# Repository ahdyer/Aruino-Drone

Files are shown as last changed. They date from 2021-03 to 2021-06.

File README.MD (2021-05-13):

## Arduino-Drone

### Description
STM32 based flight controller, developed as a final year project for the university of bath<br />

### Starting
To download this project to your computer:
1. Install GIT: https://git-scm.com/downloads
1. Go into your main project directory, open commad line and run:<br />
`git clone https://github.com/your_username/TBRe21-TSAL.git` <br />
Alternativley Install https://desktop.github.com/ and setup a local repoistory

### Using Git in Altium
1. **Save:** Once you make any changes, save the file or project
1. **Commit:** Right click on the file or project, then Version Control -> Commit. Add a note what changes you have done. This will be still local until you push the changes. See the next step.
1. **Push:** When you would like to upload all the changes to github, right click on the file / project -> Version Control -> Push
1. **Check:** Go to your github to see if everything was uploaded correctly

### Download the latest changes
If you would like to download the latest files from Github, then:<br />
1. `git fetch` # this will download the latest files from Github to your local computer<br />
2. Alternativley Install https://desktop.github.com/ and press the fetch button

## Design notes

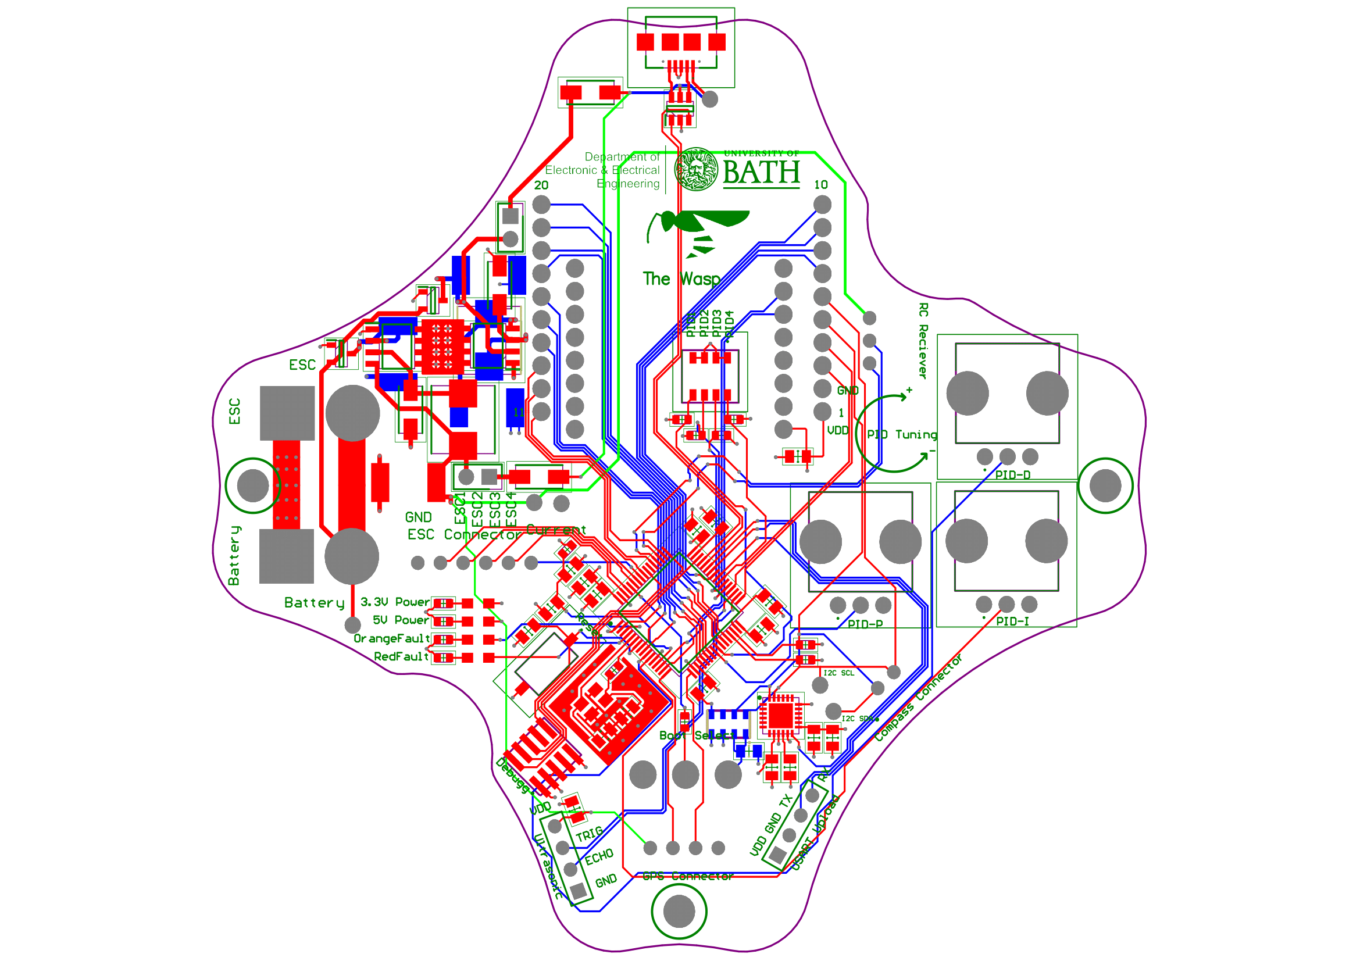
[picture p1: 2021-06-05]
STM32 Flight Controller/Schematic PNGs/STM32 Flight Controller-6.png

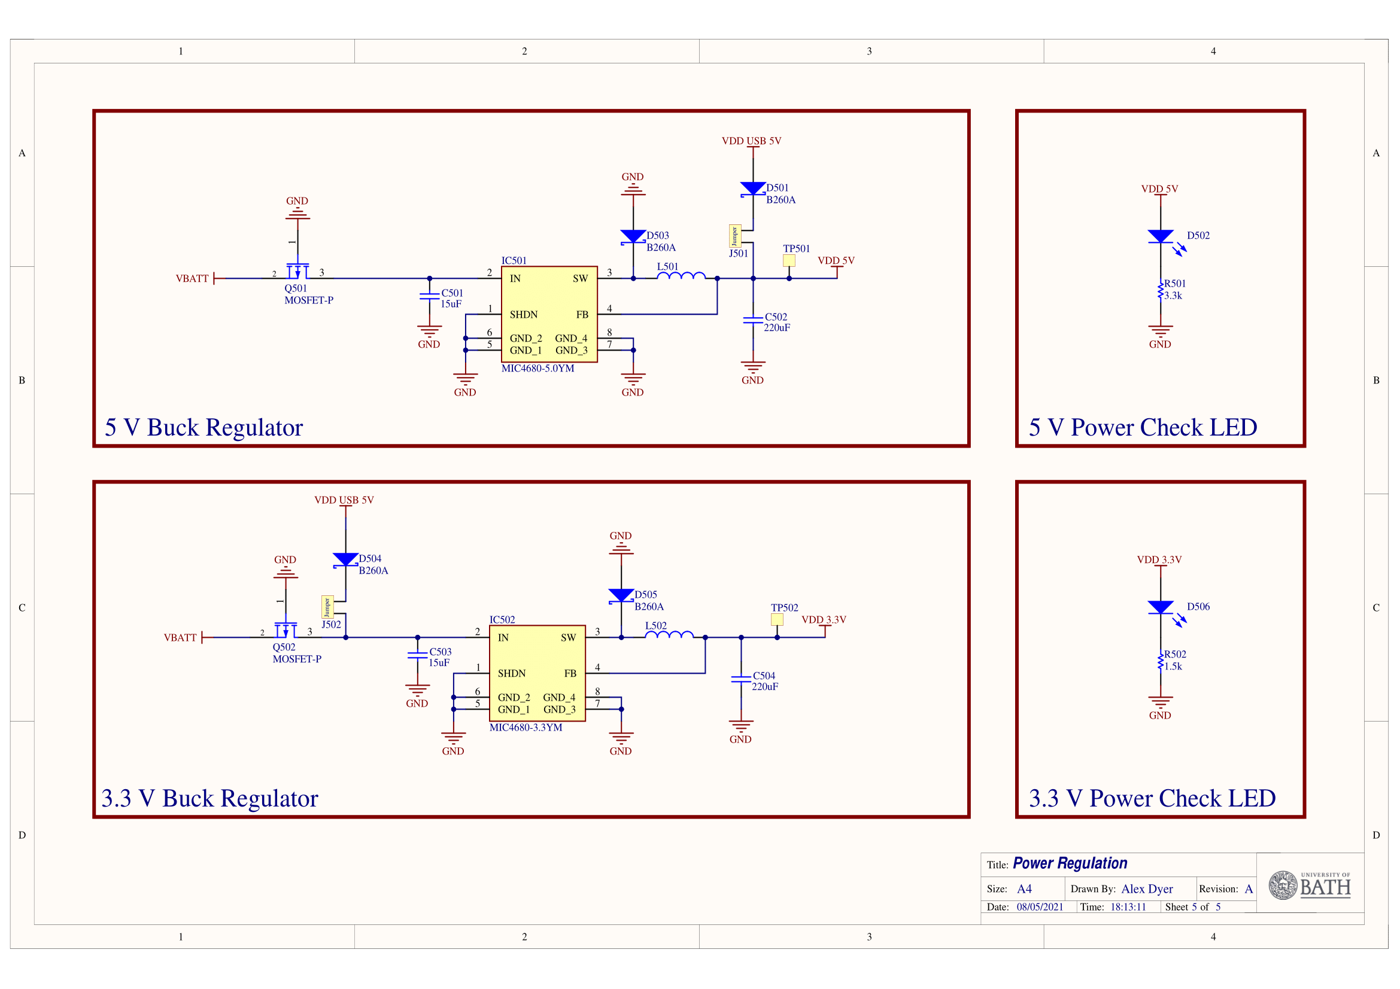
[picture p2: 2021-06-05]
STM32 Flight Controller/Schematic PNGs/STM32 Flight Controller-5.png

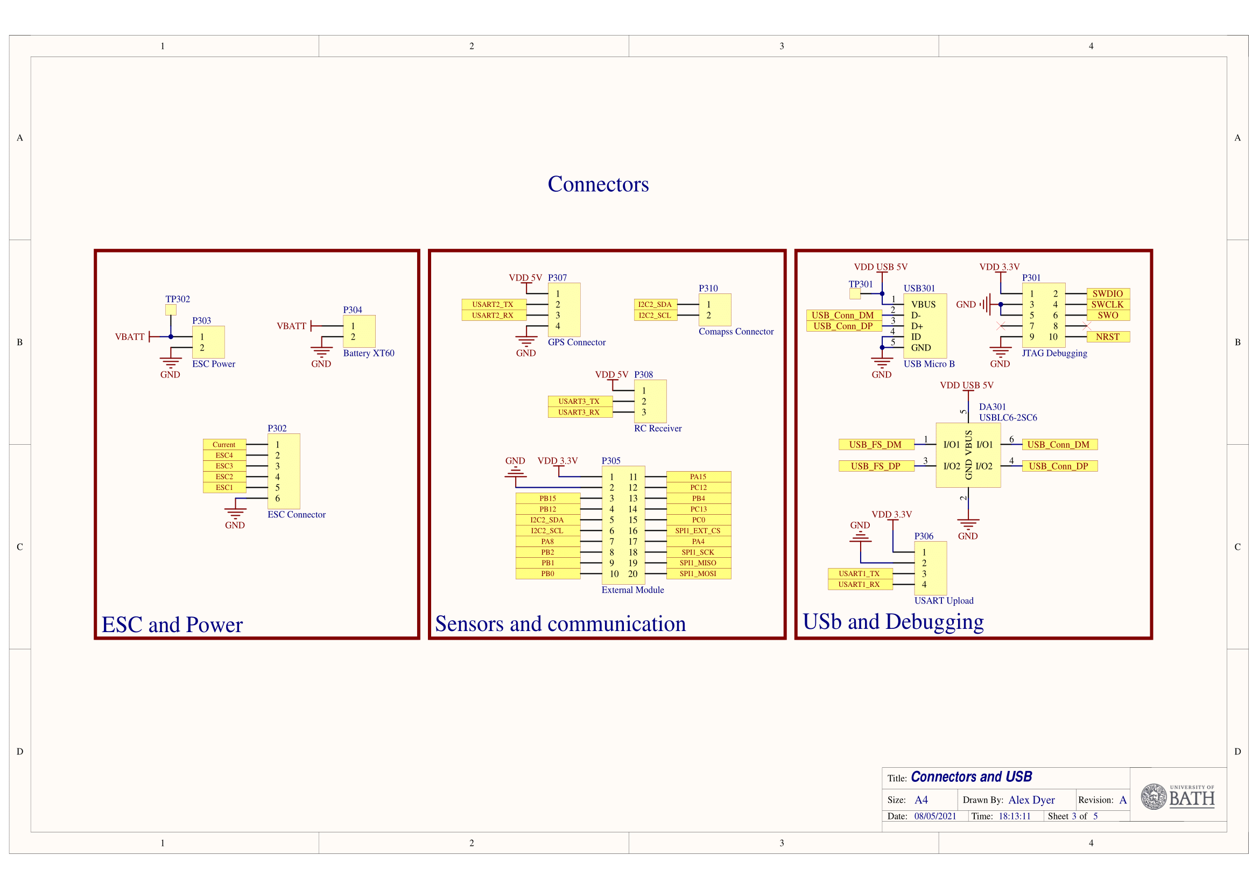
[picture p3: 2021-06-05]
STM32 Flight Controller/Schematic PNGs/STM32 Flight Controller-3.png

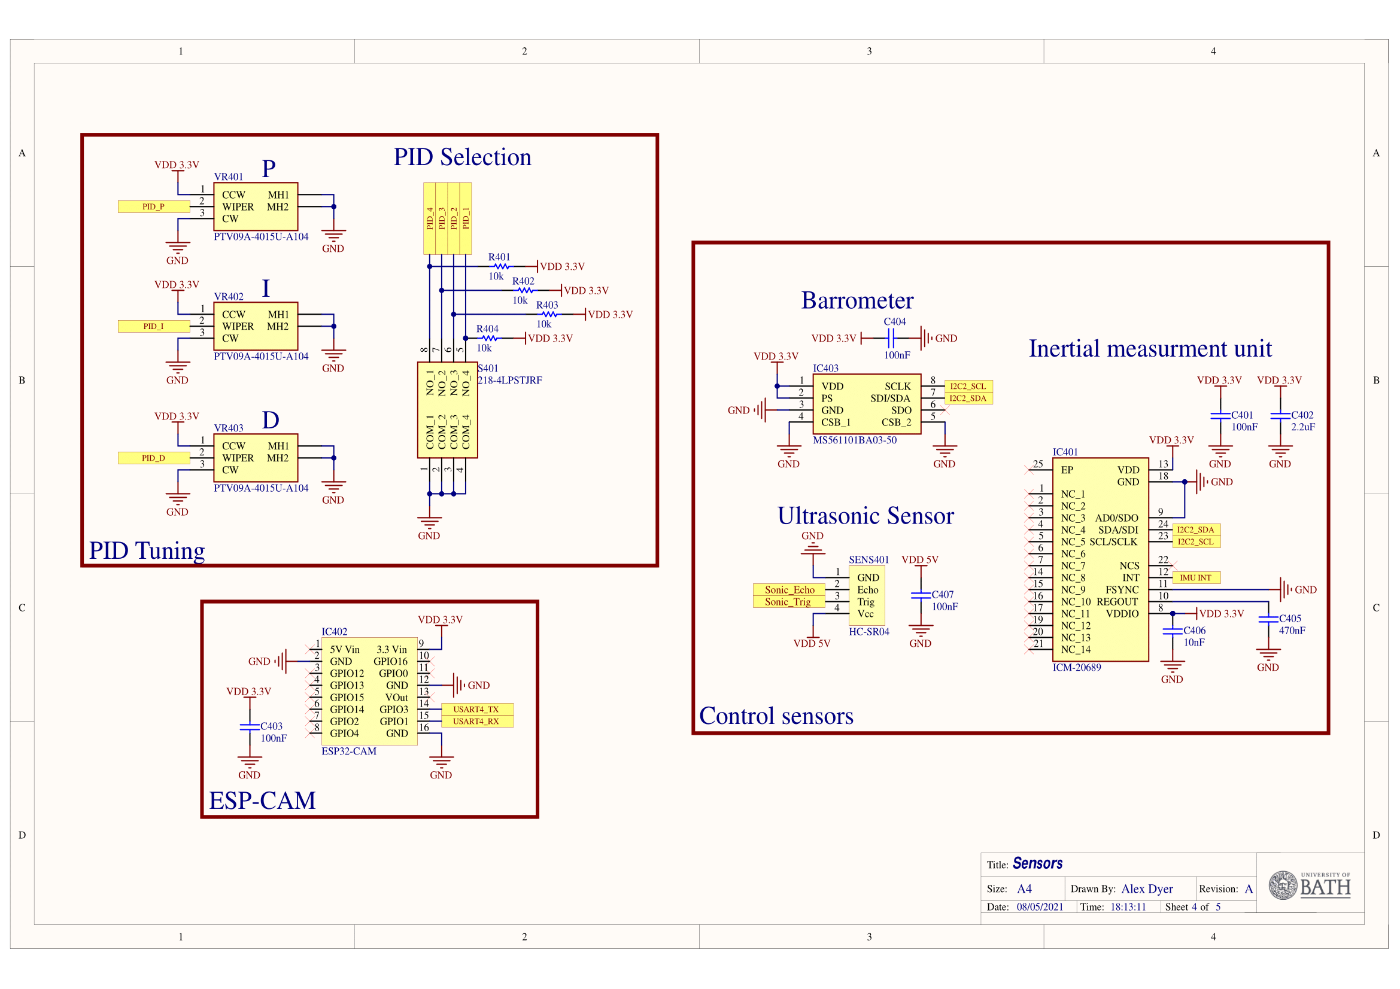
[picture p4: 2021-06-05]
STM32 Flight Controller/Schematic PNGs/STM32 Flight Controller-4.png

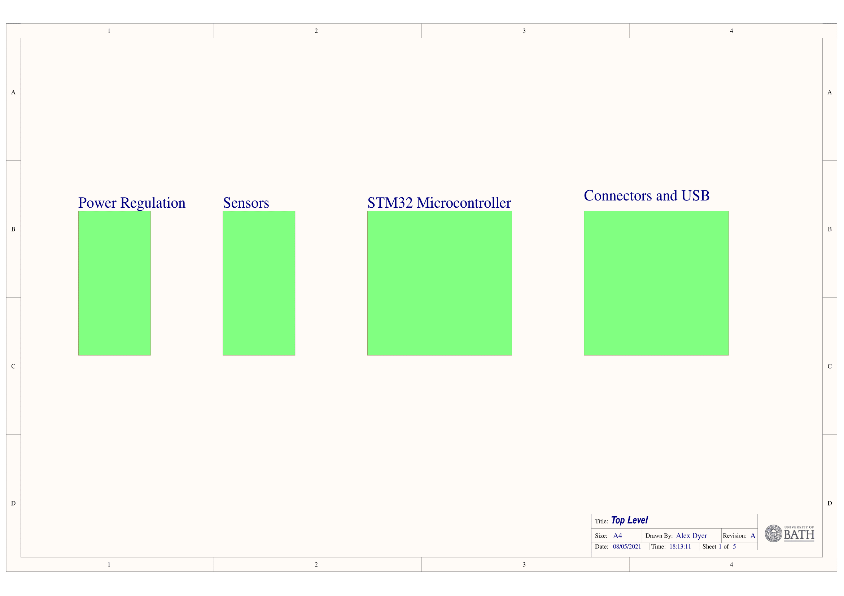
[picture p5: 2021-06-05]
STM32 Flight Controller/Schematic PNGs/STM32 Flight Controller-1.png

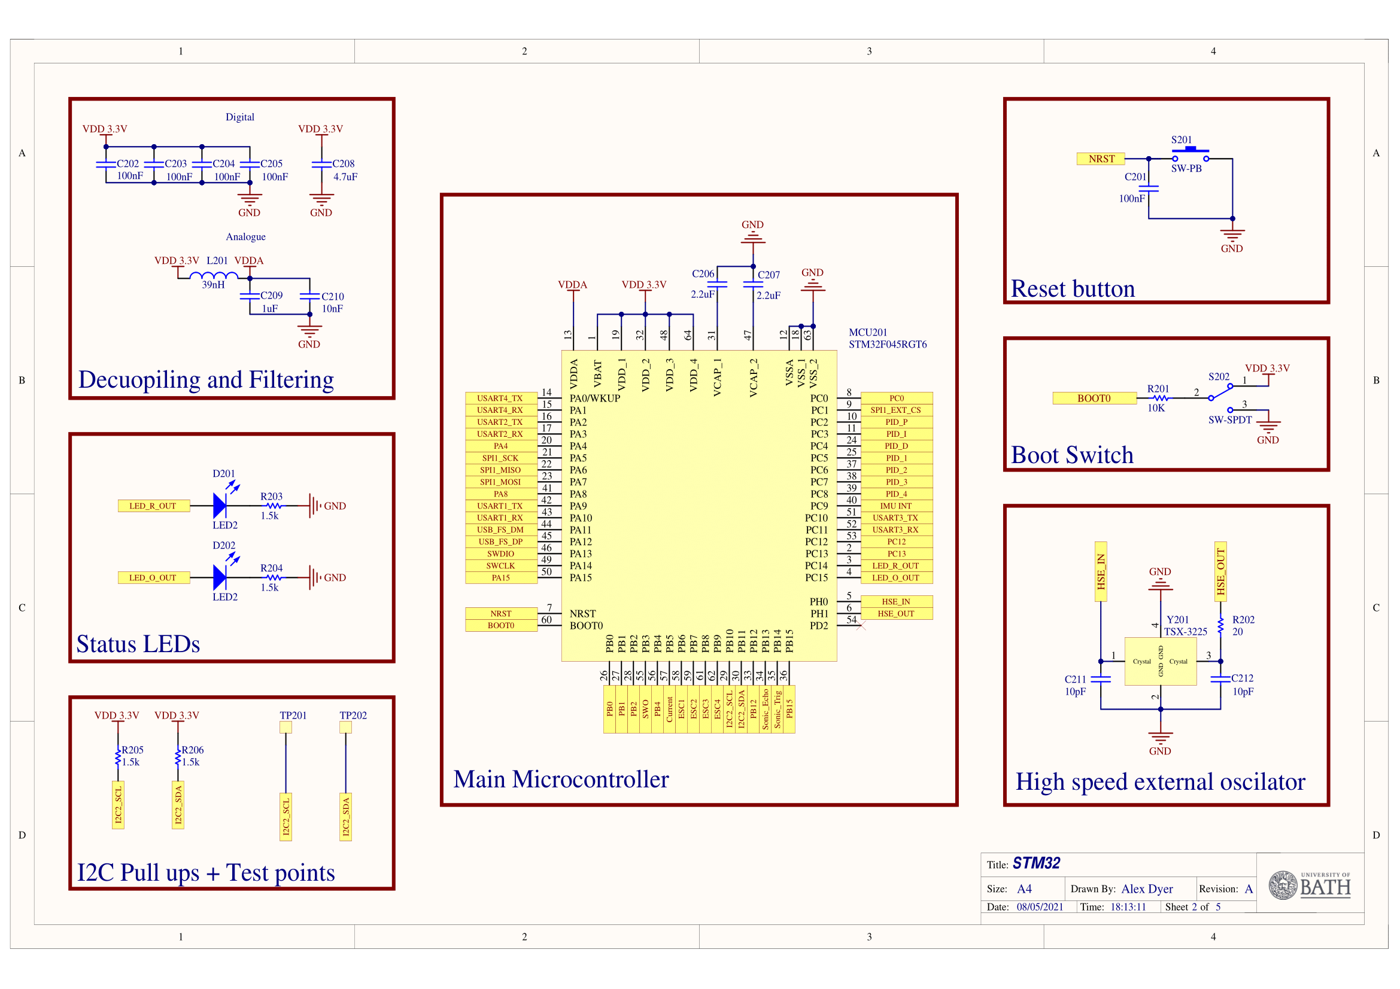
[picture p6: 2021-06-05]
STM32 Flight Controller/Schematic PNGs/STM32 Flight Controller-2.png

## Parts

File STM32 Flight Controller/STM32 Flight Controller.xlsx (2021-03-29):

Comment | Description | Designator | Footprint | LibRef | Quantity | Value | Purchase | TBRe Resistors
Cap | Capacitor | C201, C202, C203, C204, C205, C401, C403, C404, C407 | 0805 Cap | Cap | 9 | 100nF | https://uk.rs-online.com/web/p/mlccs-multilayer-ceramic-capacitors/6480957/
Cap | Low ESR Capacitor | C206, C207, C402 | 0805 Cap | Cap | 3 | 2.2uF | https://uk.rs-online.com/web/p/mlccs-multilayer-ceramic-capacitors/7883048/
Cap | Capacitor | C208 | 0805 Cap | Cap | 1 | 4.7uF | https://uk.rs-online.com/web/p/mlccs-multilayer-ceramic-capacitors/7883041/
Cap | Capacitor | C209 | 0805 Cap | Cap | 1 | 1uF | https://uk.rs-online.com/web/p/mlccs-multilayer-ceramic-capacitors/7883054/
Cap | Capacitor | C210 | 0805 Cap | Cap | 1 | 10nF | https://uk.rs-online.com/web/p/mlccs-multilayer-ceramic-capacitors/6983462/
Cap | Capacitor | C211, C212 | 0805 Cap | Cap | 2 | 10pF | https://uk.rs-online.com/web/p/mlccs-multilayer-ceramic-capacitors/6984033/
Cap | Capacitor | C405 | 0805 Cap | Cap | 1 | 470nF | https://uk.rs-online.com/web/p/mlccs-multilayer-ceramic-capacitors/6480806/
Cap | Capacitor | C406 | 0805 Cap | Cap | 1 | 10nF | https://uk.rs-online.com/web/p/mlccs-multilayer-ceramic-capacitors/6480957/
Cap | Capacitor | C501, C503 | 2917 Cap (TPSE) - duplicate | Cap | 2 | 15uF | https://www.mouser.co.uk/ProductDetail/AVX/TCJD156M050R0150E
Cap | Capacitor | C502, C504 | 2917 Cap (TJSD) | Cap | 2 | 220uF | https://www.mouser.co.uk/ProductDetail/AVX/TPSE227M016R0100V
LED2 | Typical RED, GREEN, YELLOW, AMBER GaAs LED | D201 | SML-211 Series | LED2 | 1 |  | https://uk.rs-online.com/web/p/leds/7007907/
LED2 | Typical RED, GREEN, YELLOW, AMBER GaAs LED | D202, D502, D506 | SML-211 Series | LED2 | 3 |  | https://uk.rs-online.com/web/p/leds/7007897/
B260A | Schottky Diode | D501, D503, D504, D505 | SMA (DO-214AC) | D Schottky | 4 |  | https://www.mouser.co.uk/ProductDetail/Diodes-Incorporated/B260A-13-F?qs=9XwZYT68TnR%252B3fnyovGFLA%3D%3D
USBLC6-2SC6 | TMicroelectronics USBLC6-2SC6, Dual-Element Uni-Directional TVS Diode Array, 6-Pin SOT-23 | DA301 | SOT95P280X145-6N | USBLC6-2SC6 | 1 |  | https://uk.rs-online.com/web/p/tvs-diodes/6247693/
ICM-20689 | Integrated Circuit | IC401 | QFN50P400X400X95-25N-D | ICM-20689 | 1 |  | https://www.mouser.co.uk/ProductDetail/TDK-InvenSense/ICM-20689?qs=u4fy%2FsgLU9NcfLrncAE%252BeQ%3D%3D
ESP32-CAM |  | IC402 | ESP-CAM | ESP-CAM | 1
MS561101BA03-50 | Integrated Circuit Note, Mouser Chepaer | IC403 | MS561101BA03-50 | MS561101BA03-50 | 1 |  | https://uk.rs-online.com/web/p/pressure-sensor-ics/8937130/
MIC4680-5.0YM | Switching Voltage Regulators 1.3A SuperSwitcher (5v) | IC501 | SOIC127P599X173-8N | MIC4680-5.0YM | 1 |  | https://www.mouser.co.uk/ProductDetail/Microchip-Technology-Micrel/MIC4680-50YM-TR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
MIC4680-3.3YM | Integrated Circuit | IC502 | SOIC127P599X173-8N | MIC4680-3.3YM | 1 |  | https://www.mouser.co.uk/ProductDetail/Microchip-Technology-Micrel/MIC4680-33YM?qs=kh6iOki%2FeLEl7qvTxSy9RA==
Jumper |  | J501, J502 | 2.54mm 2 pin Jumper | Jumper | 2 |  | https://www.mouser.co.uk/ProductDetail/Molex/22-28-5027?qs=l%252BWx29wYPrz7EnZr1XjkzQ%3D%3D
Inductor | Inductor | L201 | 0603 | Inductor | 1 | 39nH | https://uk.rs-online.com/web/p/multilayer-surface-mount-inductors/7859212/
Inductor | Inductor | L501, L502 | INDPM7570X540N | Inductor | 2 |  | https://www.mouser.co.uk/ProductDetail/TDK/SPM7054VT-680M-D?qs=BJlw7L4Cy7%2F5GJUhXb8MnA%3D%3D
STM32F045RGT6 |  | MCU201 | QFP50P1200X1200X160-64N | STM32F045RGT6 | 1 |  | https://uk.rs-online.com/web/p/microcontrollers/7926013/
JTAG Debugging | Samtec, FTSH, 10 Way, 2 Row, Straight Pin Header | P301 | TFTSH 1.27mm 10 way | Header 5X2 | 1 |  | https://uk.rs-online.com/web/p/pcb-headers/0451736/
ESC Connector | Header, 6-Pin | P302 | B6B-XH-A | Header 6 | 1 |  | https://uk.farnell.com/jst-japan-solderless-terminals/b6b-xh-a-lf-sn/connector-header-tht-2-5mm-6way/dp/1516282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
ESC Power | Header, 2-Pin | P303 | Female XT60 | Header 2 | 1 |  | https://hobbyking.com/en_us/nylon-xt60-connectors-male-female-5-pairs-genuine.html?___store=en_us
Battery XT60 | Header, 2-Pin | P304 | Female XT60 | Header 2 | 1 |  | https://hobbyking.com/en_us/nylon-xt60-connectors-male-female-5-pairs-genuine.html?___store=en_us
External Module | External Module | P305 | External Module | Header 10X2A | 1 |  | https://www.mouser.co.uk/ProductDetail/Samtec/CES-110-02-G-S?qs=0lQeLiL1qyZeC2zaPJHALg%3D%3D
USART Upload | Header, 4-Pin | P306 | HDR1X4 | Header 4 | 1 |  | https://www.mouser.co.uk/ProductDetail/Amphenol-Commercial-Products/G800W304018EU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
GPS Connector | Header, 4-Pin | P307 | B4B-XH-A | Header 4 | 1 |  | https://uk.farnell.com/jst-japan-solderless-terminals/b4b-xh-a-lf-sn/header-vertical-4way/dp/1516278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
RC Receiver | Header, 3-Pin | P308 | B3B-XH-A | Header 3 | 1 |  | https://uk.farnell.com/jst-japan-solderless-terminals/b3b-xh-a-lf-sn/header-vertical-3way/dp/1516277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
Comapss Connector | Compass Connector | P310 | B2B-XH-A | Header 2 | 1 |  | https://uk.farnell.com/jst-japan-solderless-terminals/b2b-xh-a-lf-sn/header-vertical-2way/dp/1516276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
MOSFET-P | P-Channel MOSFET | Q501, Q502 | SOT95P230X110-3N | MOSFET-P | 2 |  | https://www.mouser.co.uk/ProductDetail/Nexperia/PMV250EPEAR?qs=Yna0arPQ0CTtAa8k6X9CyQ%3D%3D
0603 | Resistor | R201 | 0603 | Res1 | 1 | 10K | https://uk.rs-online.com/web/p/mlccs-multilayer-ceramic-capacitors/2644236/
0603 | Resistor | R202 | 0603 | Res1 | 1 | 20 | https://uk.rs-online.com/web/p/surface-mount-fixed-resistors/6661904/
0603 | Resistor | R203, R204, R205, R206, R502 | 0603 | Res1 | 5 | 1.5k | https://uk.rs-online.com/web/p/mlccs-multilayer-ceramic-capacitors/2644236/
0603 | Resistor | R401, R402, R403, R404 | 0603 | Res1 | 4 | 10k | https://uk.rs-online.com/web/p/surface-mount-fixed-resistors/9013601/
0603 | Resistor | R501 | 0603 | Res1 | 1 | 3.3k | https://uk.rs-online.com/web/p/mlccs-multilayer-ceramic-capacitors/2644236/
SW-PB | Switch | S201 | PTS636SM25JSMTRLFS | SW-PB | 1 |  | https://www.mouser.co.uk/ProductDetail/CK/PTS636-SM25J-SMTR-LFS?qs=vLWxofP3U2zGz0hgscFyyw%3D%3D
SW-SPDT | SPDT Subminiature Toggle Switch, Right Angle Mounting, Vertical Actuation | S202 | Slide Switch | SW-SPDT | 1 |  | https://uk.rs-online.com/web/p/slide-switches/7347334/
218-4LPSTJRF | DIP Switches/SIP Switches SURFACE MOUNT, GOLD, HALF-PITCH DIP SWITCH, 4-POLE, LOW PROFILE ACTUATOR, BOTTOM SEAL, TAPE SEAL, J-BEND, REEL, OFF | S401 | 2184LPSTJRF | 218-4LPSTJRF | 1 |  | https://www.mouser.co.uk/ProductDetail/CTS-Electronic-Components/218-4LPSTJRF
HC-SR04 | Ultrasonic Distance Sensor | SENS401 | HDR1X4 | Header 4 | 1 |  | https://www.sparkfun.com/products/15569
Test Point |  | TP201, TP202, TP301, TP302, TP501, TP502 | Test Point THT 1mm | Test Point | 6 |  | https://uk.rs-online.com/web/p/terminal-posts/2622179/?searchHistory=%7B%22enabled%22%3Atrue%7D\
USB Micro B | Molex USB Connector, SMT, Socket 2.0 B, Solder, Right Angle | USB301 | UJ2MIBHGSMTTR | USB Micro B | 1 |  | https://www.mouser.co.uk/ProductDetail/CUI-Devices/UJ2-MIBH-G-SMT-TR
PTV09A-4015U-A104 | Variable Resistor | VR401, VR402, VR403 | PTV09A4015UA104 | PTV09A-4015U-A104 | 3 |  | https://www.mouser.co.uk/ProductDetail/Bourns/PTV09A-4015U-A104
TSX-3225 | EPSON 16MHz Crystal Unit ±10ppm TSX-3225 4-Pin | Y201 | TSX-3225 | TSX-3225 | 1 |  | https://uk.rs-online.com/web/p/crystal-units/9047516/

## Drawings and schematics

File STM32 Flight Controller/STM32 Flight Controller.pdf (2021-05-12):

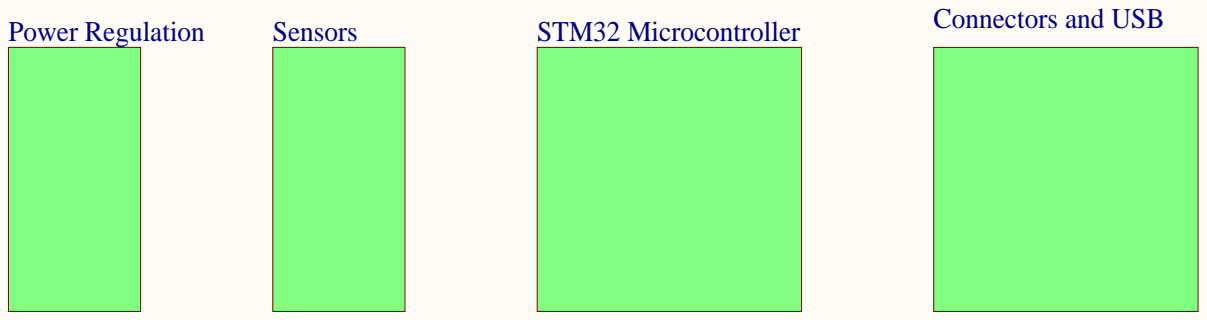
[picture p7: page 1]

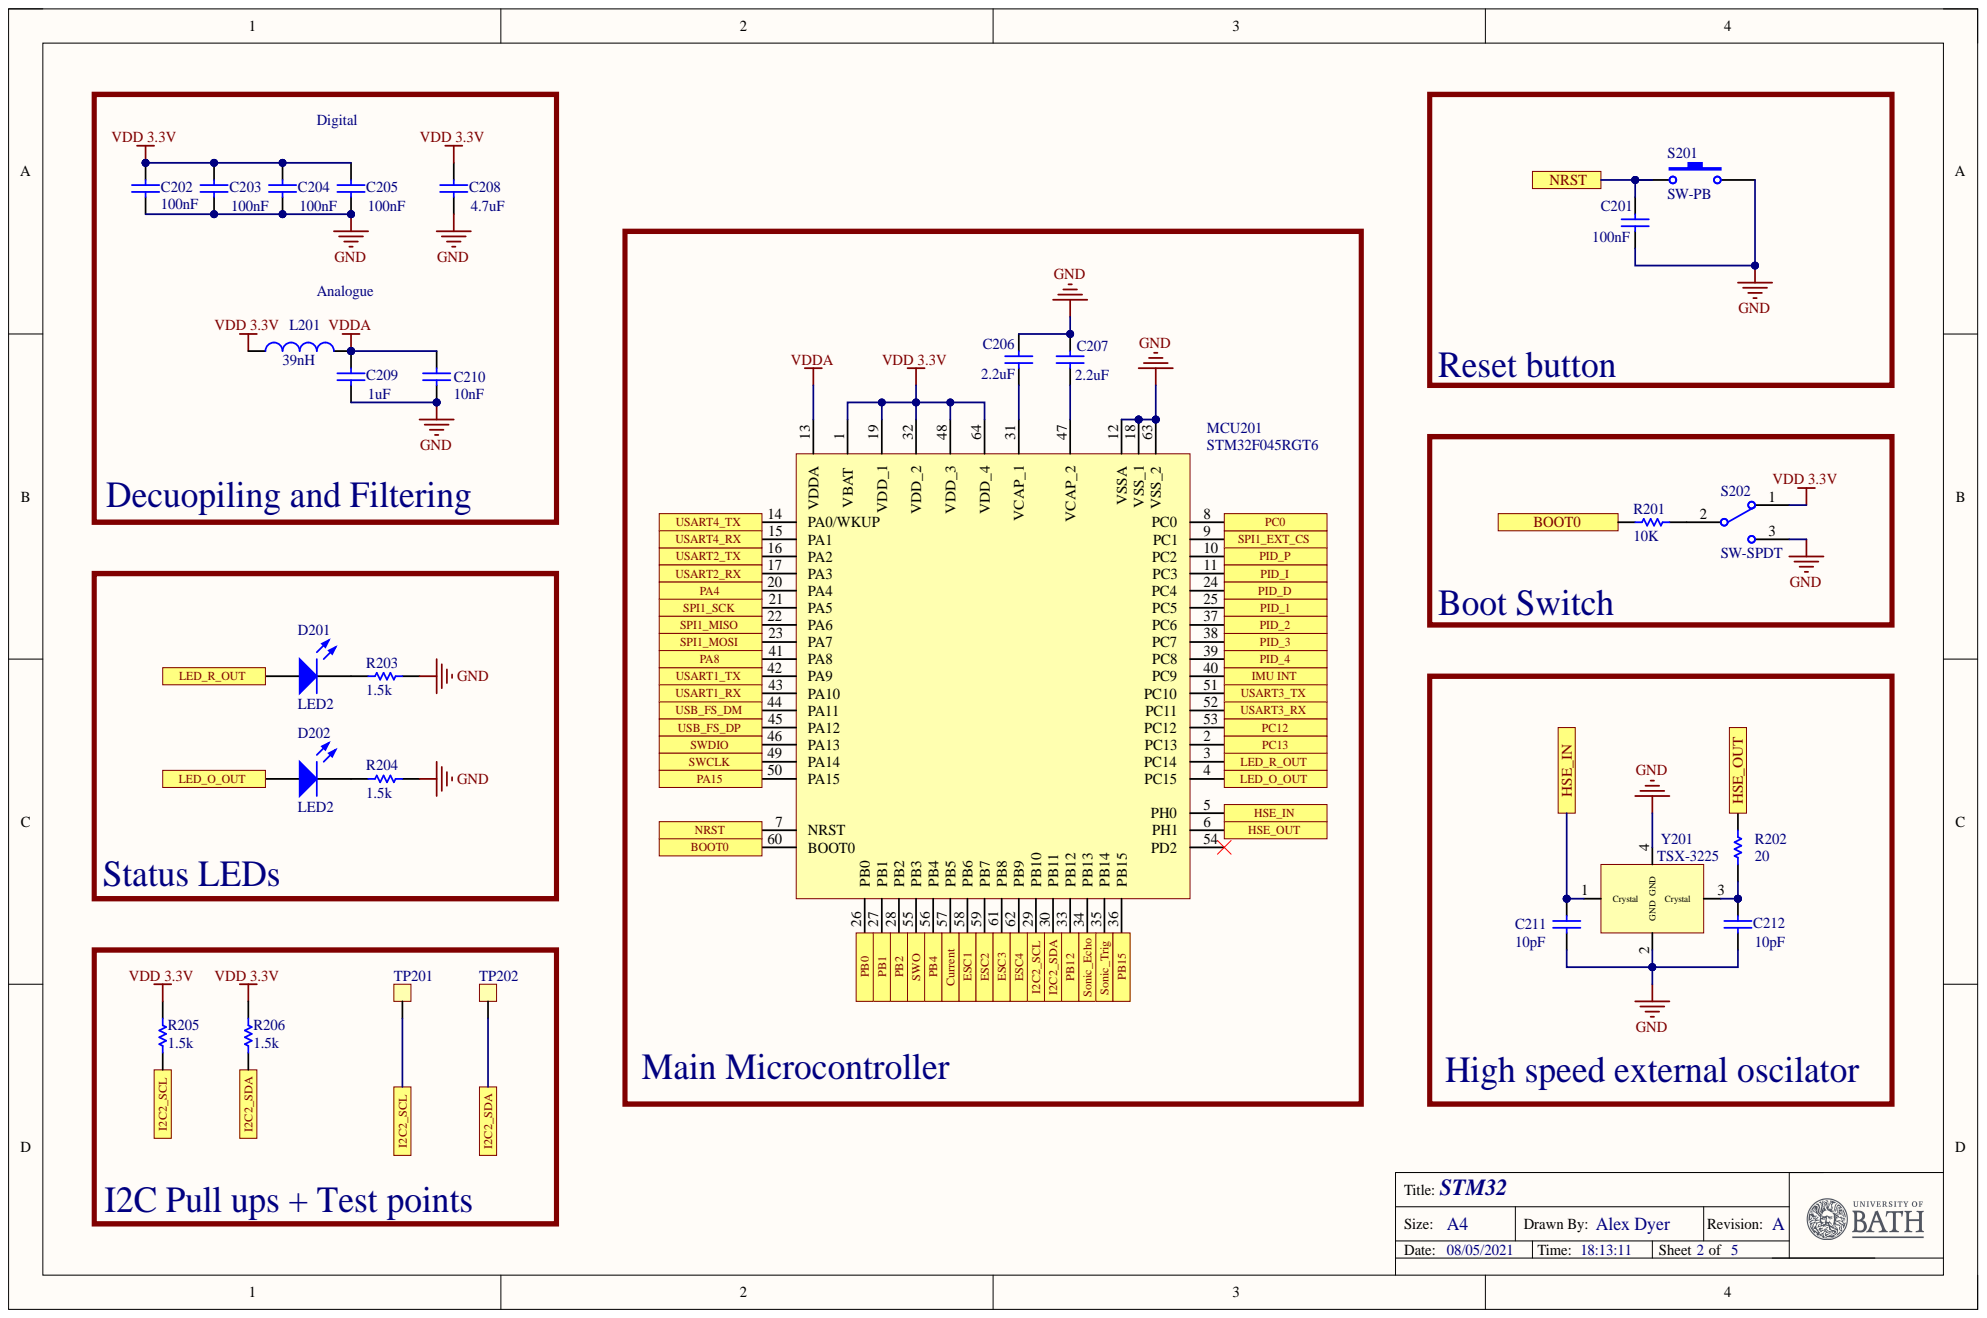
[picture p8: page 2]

SPI1_MISO | PID_2
SPI1_MOSI | PID_3

USB_FS_DM | USART3_RX
USB_FS_DP | PC12

I2C Pull ups + Test points

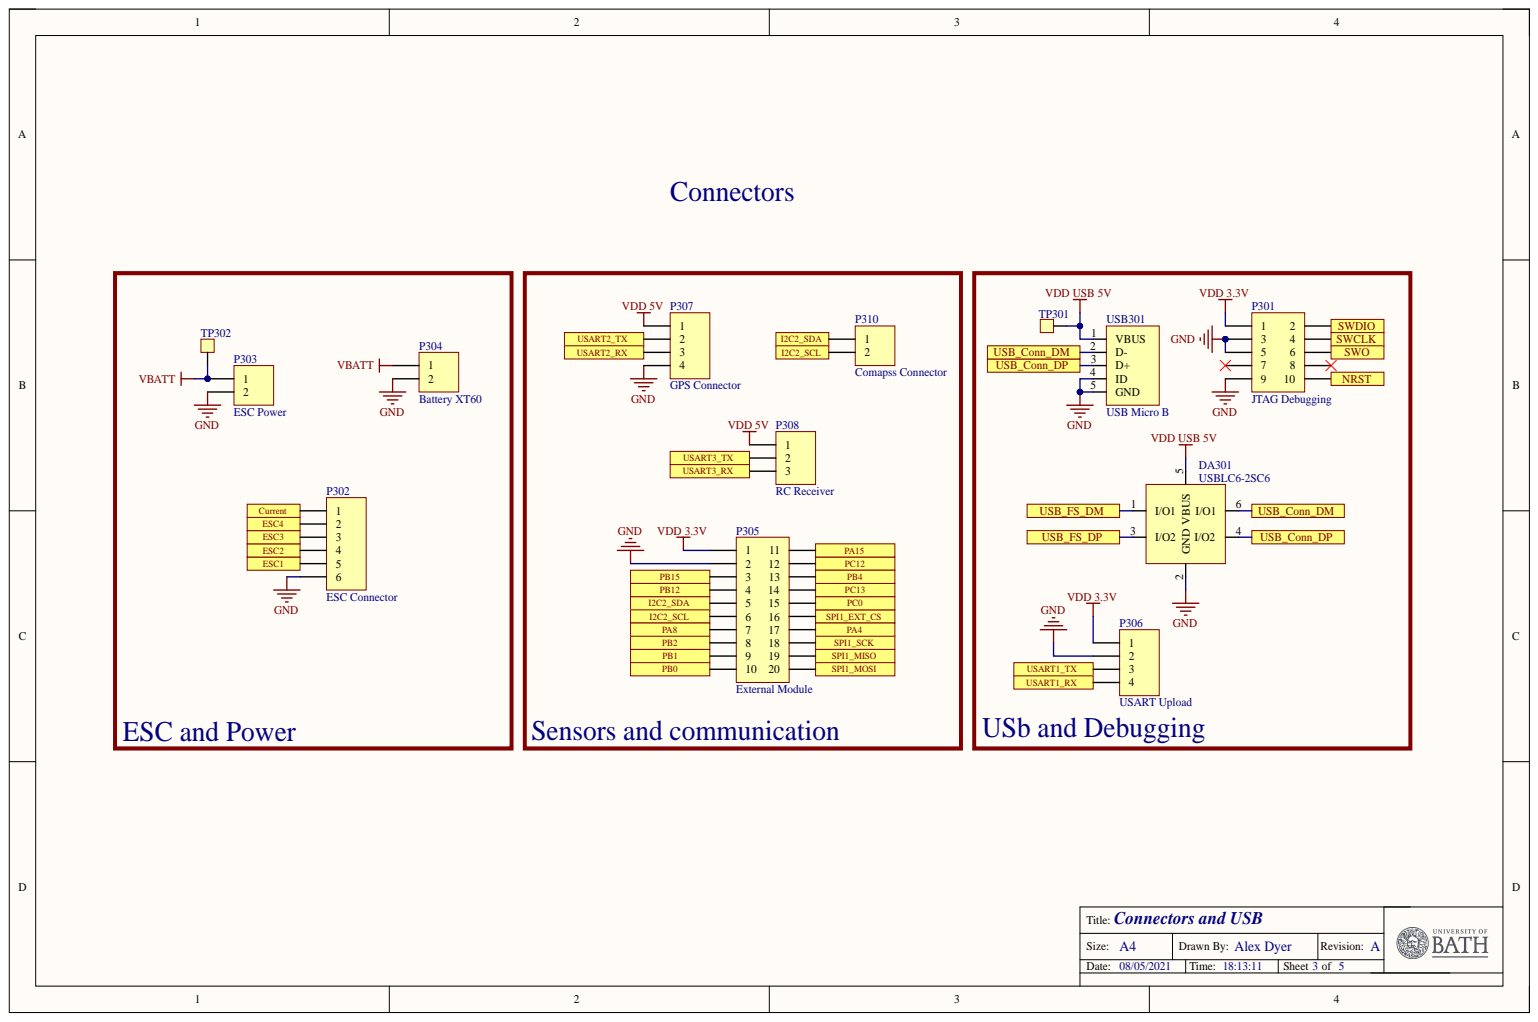
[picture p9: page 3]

I2C2_SCL | SPI1_EXT_CS
PA8 | PA4

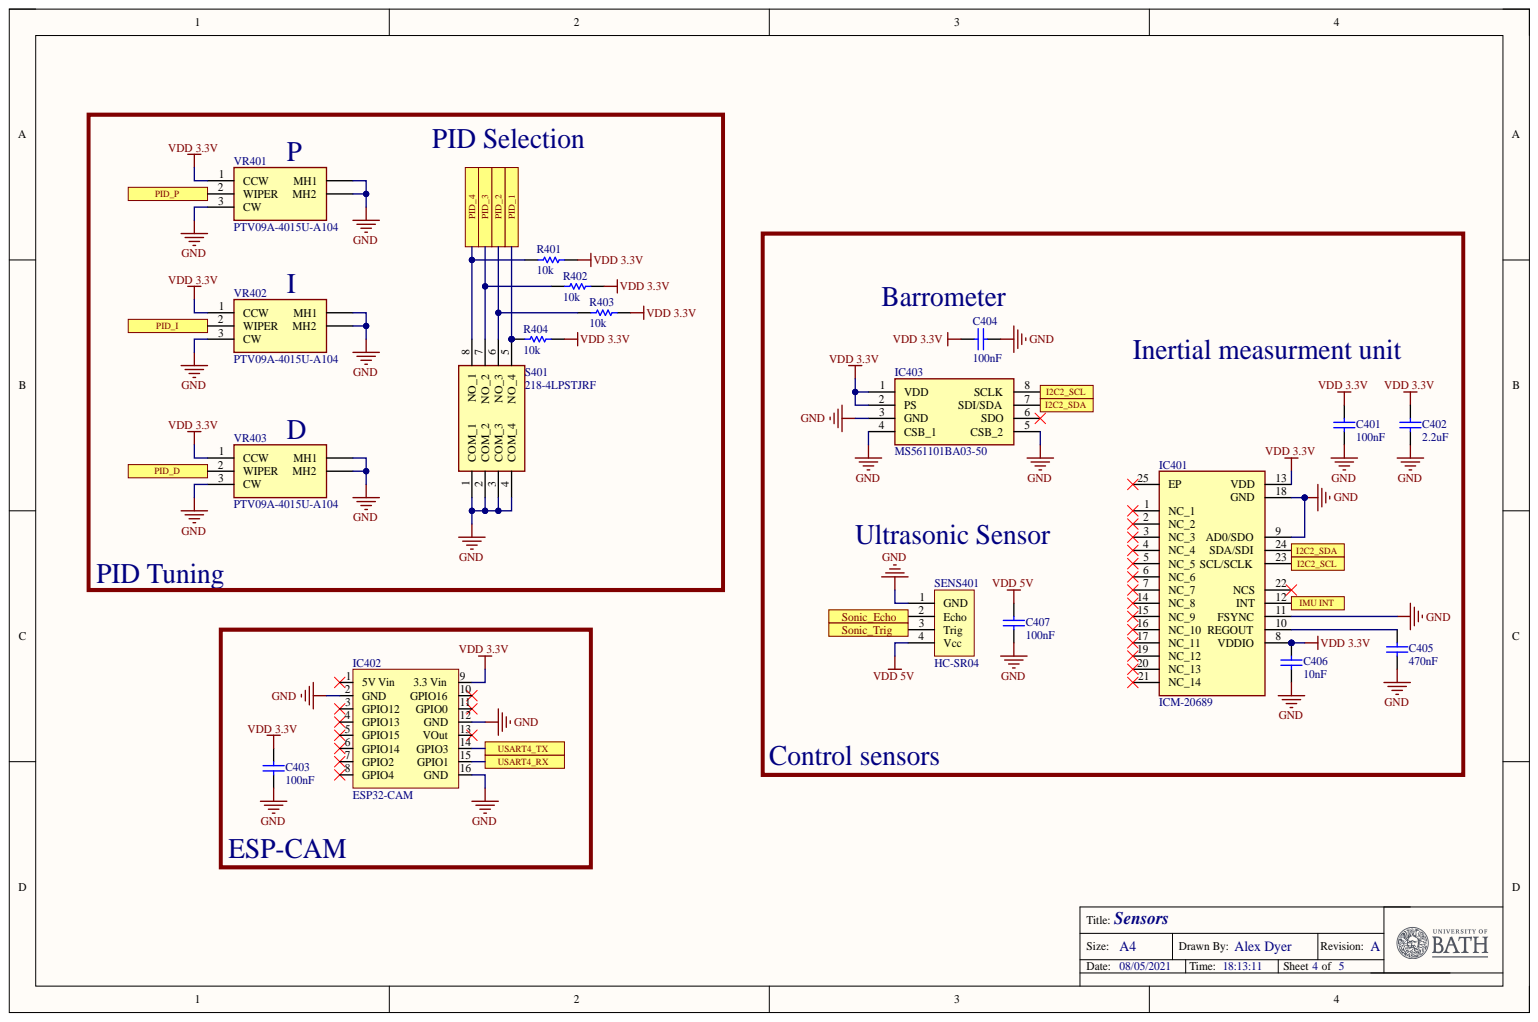
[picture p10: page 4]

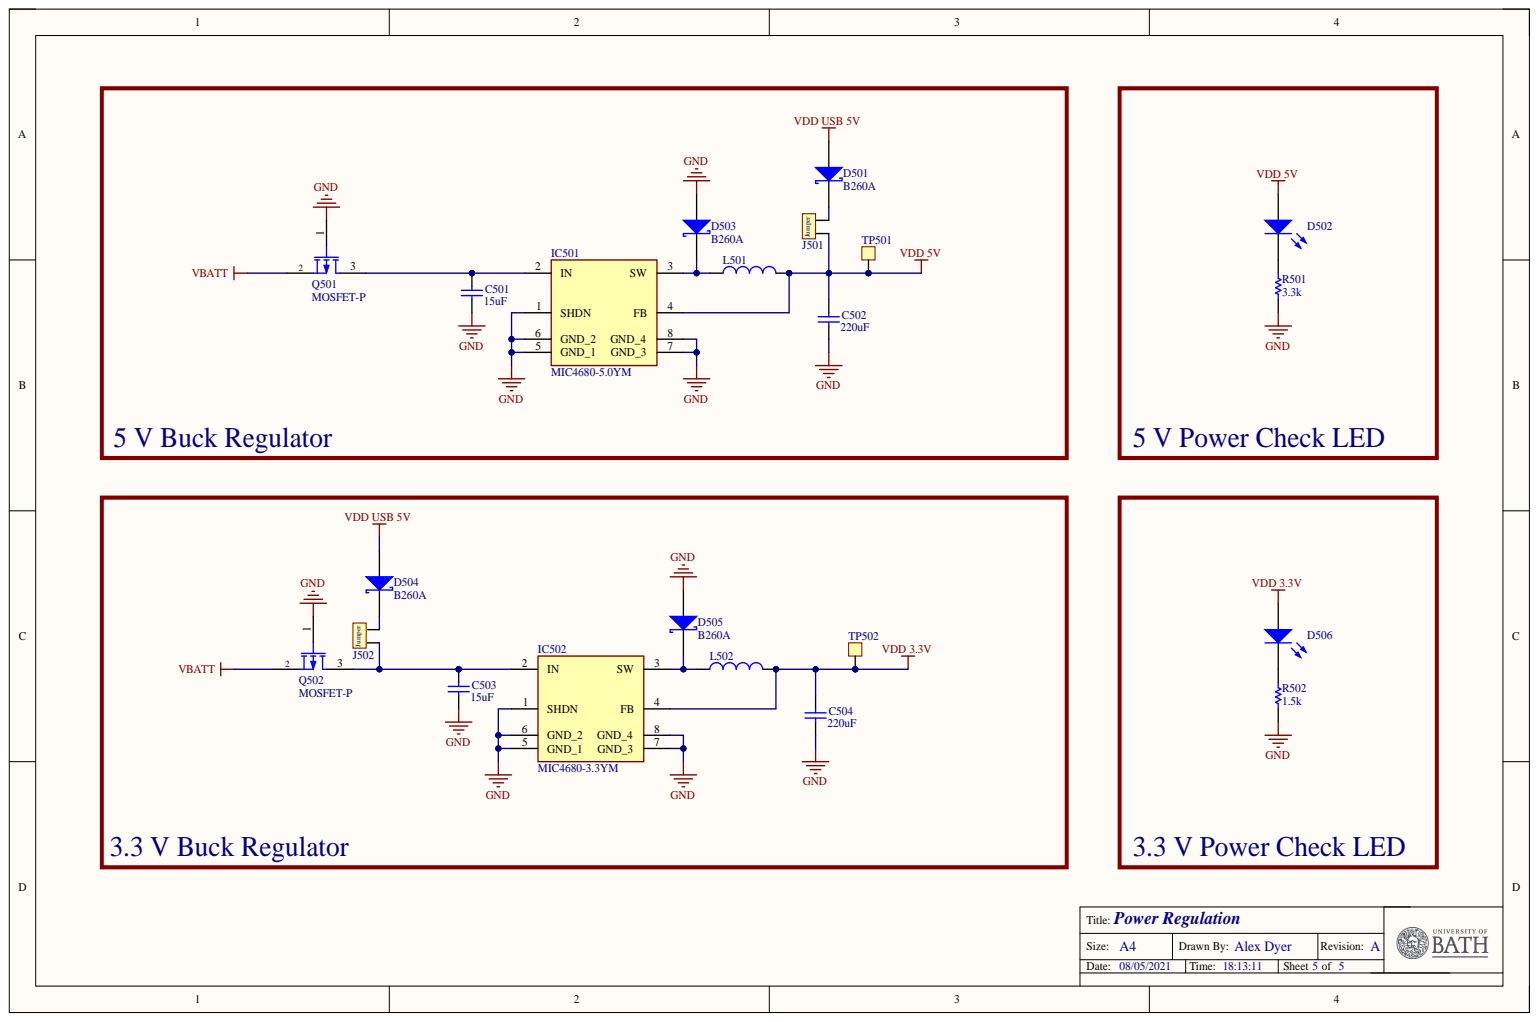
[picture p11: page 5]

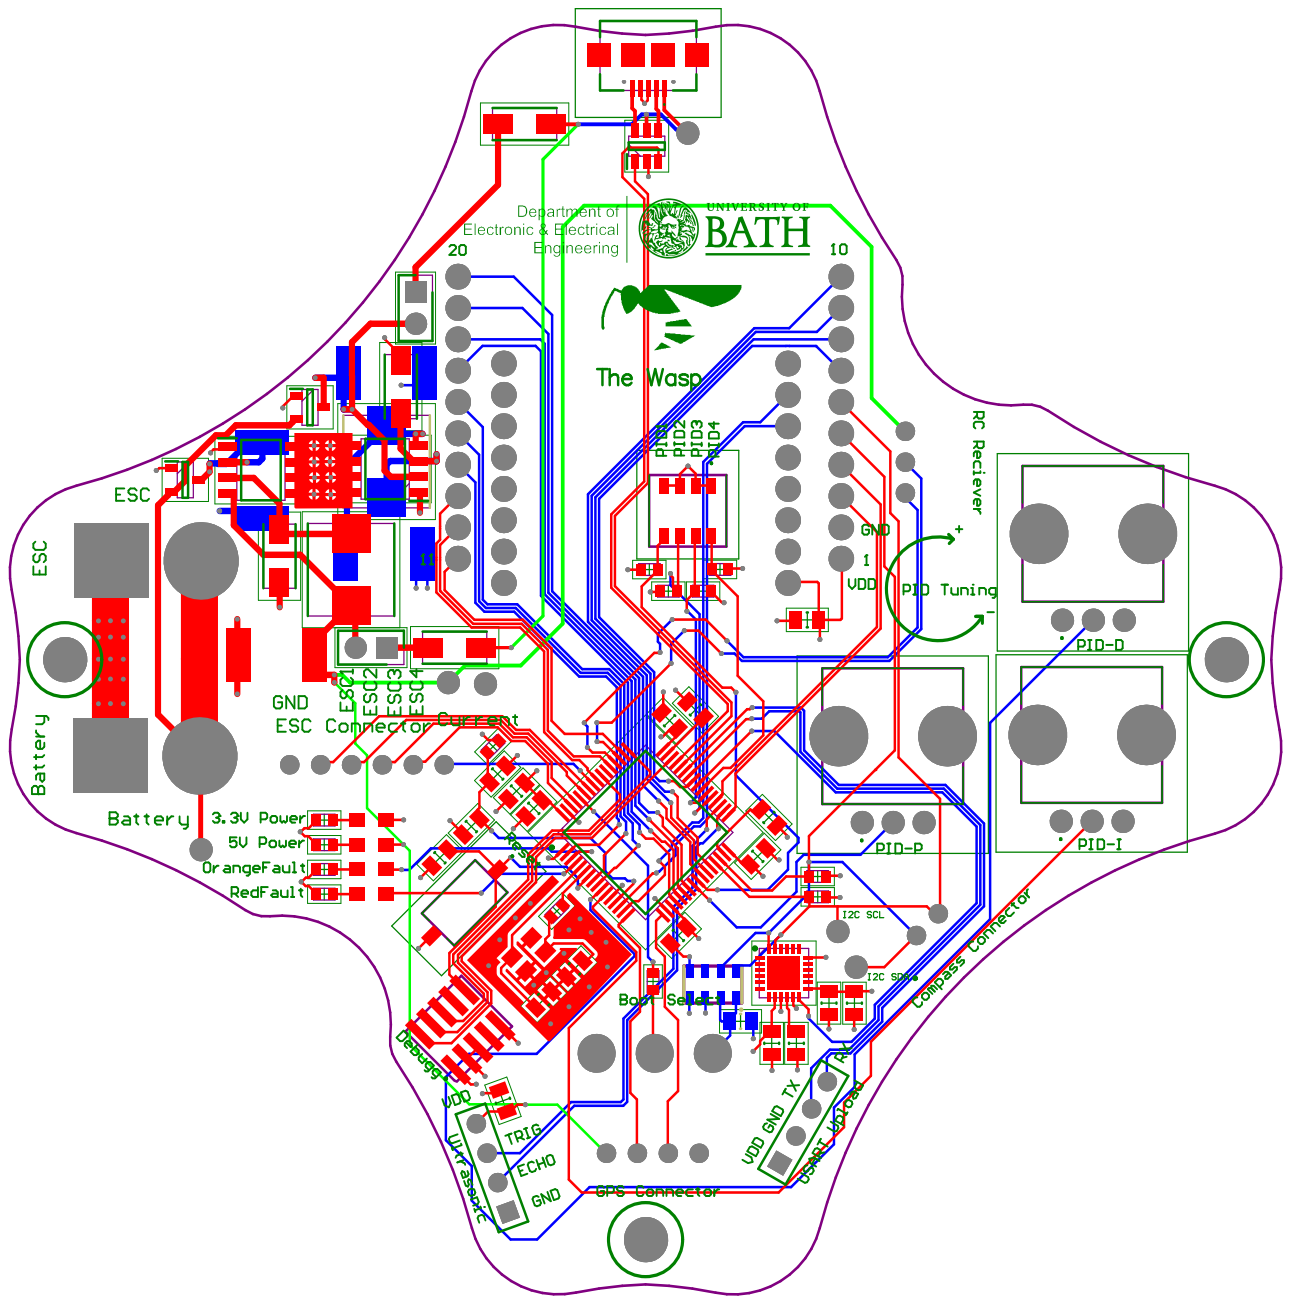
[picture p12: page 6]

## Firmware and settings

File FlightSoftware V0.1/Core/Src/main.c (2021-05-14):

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
/* Includes ------------------------------------------------------------------*/
#include "main.h"

/* USER CODE BEGIN Includes */
#include "math.h"

/* USER CODE END Includes */

I2C_HandleTypeDef hi2c2;

TIM_HandleTypeDef htim1;
TIM_HandleTypeDef htim2;
TIM_HandleTypeDef htim4;
TIM_HandleTypeDef htim12;

UART_HandleTypeDef huart3;
DMA_HandleTypeDef hdma_usart3_rx;

/* USER CODE BEGIN PV */
// RC Receiver Channels
// Array to store all Channels
int16_t channel[10];
// Channel[0] = Roll
// Channel[1] = Pitch
// Channel[2] = Throttle
// Channel[3] = Yaw
// Channel[4] = Arm Switch
// Channel[5] = Mode Switch

// PID Variables
float max_rotate = 200;
//X - Pitch | Y - Roll | Z - Yaw
// Roll
float pid_p_roll = 1;
float pid_i_roll = 0;
float pid_d_roll = 10;
float pid_gy_roll = 0, pid_setpoint_roll = 0, pid_output_roll = 0, pid_prev_err_roll = 0, pid_integ_roll = 0;
float roll_al = 0; // autolevel for roll
// Pitch
// uses same PID values as roll
float pid_gy_pitch = 0, pid_setpoint_pitch = 0, pid_output_pitch = 0, pid_prev_err_pitch = 0, pid_integ_pitch = 0;
float pitch_al = 0; // autolevel for pitch
// Yaw
float pid_p_yaw = 1;
float pid_i_yaw = 0.01;
float pid_d_yaw = 0;
float pid_gy_yaw = 0, pid_setpoint_yaw = 0, pid_output_yaw = 0, pid_prev_err_yaw = 0, pid_integ_yaw = 0;

uint16_t arm = 0;

uint16_t esc_1, esc_2, esc_3, esc_4;
uint16_t motor_idle = 1100;


// HC-SR04 Variables
uint16_t echo_edge_1 = 0;
uint16_t echo_edge_2 = 0;
float height = 0;
uint8_t capture_num = 0;
// speed of sound in cm / uS divided by 2 as we get round trip distance
const float time_to_dist = 0.0343/2;

enum flight_states{
	error,
	idle,
	arming,
	rate_mode,
	auto_level,
	altitude_hold
};

enum flight_states flight_state = idle;



// Flags
// Flag to show both edges of the HC-SR04 echo have been measured
uint8_t sr_rdy_flg = 0;
// Safety Flags
uint8_t fault_flag = 0;


/* USER CODE END PV */

void SystemClock_Config(void);
static void MX_GPIO_Init(void);
static void MX_DMA_Init(void);
static void MX_I2C2_Init(void);
static void MX_TIM1_Init(void);
static void MX_USART3_UART_Init(void);
static void MX_TIM4_Init(void);
static void MX_TIM12_Init(void);
static void MX_TIM2_Init(void);
/* USER CODE BEGIN PFP */
float ABS(float x);

HAL_StatusTypeDef ICM20689_Read(uint8_t address, float *acc_x, float *acc_y, float *acc_z, float *temp,
								float *gy_x, float *gy_y, float *gy_z, float gy_cal_x, float gy_cal_y,
								float gy_cal_z, float acc_cal_x, float acc_cal_y, float acc_cal_z);

HAL_StatusTypeDef ICM20689_Config(uint8_t address, float *gy_cal_x, float *gy_cal_y, float *gy_cal_z, float *acc_cal_x, float *acc_cal_y, float *acc_cal_z);

void Update_Motors();

void Calculate_PIDs();

void Calculate_SetPoints();

void HC_SR04_Read();

void uSec_Delay(uint32_t uSec);

void Check_Faults();
//void Calculate_Angles(float acc_x, float acc_y, float acc_z, float gy_x, float gy_y, float gy_z, float *roll, float *pitch, float *yaw)
//{
//	//Function variables
//	// gyroscope and accelerometer temporary angles
//
//	// initalisation counter
//	uint8_t count = 0;
//
//
//	if (count == 0){
//		count++;
//		gy_roll = 0, gy_pitch = 0, gy_yaw = 0;
//		acc_roll = 0, acc_pitch = 0, acc_yaw = 0;
//		pid_gy_roll = 0, pid_gy_pitch = 0, pid_gy_yaw = 0;
//	}
//
//
//
//
//	// transform pitch and roll depending on yaw value
//
//	//Calculate the traveled angles from the accelerometer
//
//	//Complementary filter on angles to correct gyroscope drift
//
//
//}
/* USER CODE END PFP */

/**
  * @brief  The application entry point.
  * @retval int
  */
int main(void)
{
  /* MCU Configuration--------------------------------------------------------*/

  /* Reset of all peripherals, Initializes the Flash interface and the Systick. */
  HAL_Init();

  /* Configure the system clock */
  SystemClock_Config();

  /* Initialize all configured peripherals */
  MX_GPIO_Init();
  MX_DMA_Init();
  MX_I2C2_Init();
  MX_TIM1_Init();
  MX_USART3_UART_Init();
  MX_TIM4_Init();
  MX_TIM12_Init();
  MX_TIM2_Init();
  /* USER CODE BEGIN 2 */



  // ICM20689 variables
	const uint8_t icm20689_address = 0x68;
	float acc_x, acc_y, acc_z;
	float temp;
	float gy_x, gy_y, gy_z;
	// Calibration variables
	float gy_cal_x = 0, gy_cal_y = 0, gy_cal_z = 0;
	float acc_cal_x = 0, acc_cal_y = 0, acc_cal_z = 0;
	// Angle Variables
	//X - Pitch | Y - Roll | Z - Yaw
	float pitch = 0, roll = 0, yaw = 0;
	float pitch_t = 0, roll_t = 0, yaw_t = 0;
	float gy_roll = 0, gy_pitch = 0, gy_yaw = 0;
	float acc_roll = 0, acc_pitch = 0, acc_yaw = 0;
	float acc_tot_vect = 0;

	// MS5611
	const uint8_t ms5611_address = 0x77;

	uint16_t looptimmer = 0;
	uint8_t error_counter = 0;
	uint8_t armed = 0;

	uint32_t loopcounter = 0;

	//UART DMA variables
	uint8_t rx_buff[32] = {0};

	// Start DMA UART RX
	HAL_StatusTypeDef uart_status;
	uart_status = HAL_UART_Receive_DMA(&huart3, rx_buff, 32);
	// Check for errors in starting the UART


  HAL_Delay(1000); // Wait for the icm20689 to initialise
  while(rx_buff[0] != 0x20){
	  HAL_GPIO_TogglePin(GPIOC, r_led_Pin);
	  HAL_Delay(500);
  }
  ICM20689_Config(icm20689_address, &gy_cal_x, &gy_cal_y, &gy_cal_z, &acc_cal_x, &acc_cal_y, &acc_cal_z); // configure ICM power register and calibrate the gyroscope

  HAL_TIM_PWM_Start(&htim4, TIM_CHANNEL_1);
  HAL_TIM_PWM_Start(&htim4, TIM_CHANNEL_2);
  HAL_TIM_PWM_Start(&htim4, TIM_CHANNEL_3);
  HAL_TIM_PWM_Start(&htim4, TIM_CHANNEL_4);

  // Reset both status lights
  HAL_GPIO_WritePin(GPIOC, o_led_Pin, RESET);
  HAL_GPIO_WritePin(GPIOC, r_led_Pin, RESET);


  /* USER CODE END 2 */

  /* Infinite loop */
  /* USER CODE BEGIN WHILE */
  // Loop timer setup
    TIM1->CR1 |= 1<<0;
    while (!(TIM1->SR & 1<<0));
    TIM1->CNT = 0;


  while (1)
  {
    /* USER CODE END WHILE */

    /* USER CODE BEGIN 3 */

	  // Increment loop counter
	  loopcounter ++;

	  ICM20689_Read(icm20689_address, &acc_x, &acc_y, &acc_z, &temp, &gy_x, &gy_y, &gy_z, gy_cal_x, gy_cal_y, gy_cal_z, acc_cal_x, acc_cal_y, acc_cal_z);

	  //Complementary filter applied to gyroscope values
	  pid_gy_roll = (pid_gy_roll*0.7) + (gy_y *0.3);
	  pid_gy_pitch = (pid_gy_pitch*0.7) + (gy_x *0.3);
	  pid_gy_yaw = (pid_gy_yaw*0.7) + (gy_z *0.3);

	  //Calculate the travelled angles from the gyroscope
	  //loop every 1 / 250hz = 0.004
      roll = roll + (gy_y / 250);
	  pitch = pitch + (gy_x / 250);
	  gy_yaw = gy_yaw + (gy_z / 250);

	  //need to rotate pitch and roll by the sin of yaw
	  roll += (pitch * (sin(gy_z * 0.00006981)));
	  pitch -= roll * (sin(gy_z * 0.00006981));


	  // Calculate acceleration vectors
	  acc_tot_vect = sqrt((acc_x*acc_x)+(acc_y*acc_y)+(acc_z*acc_z));
	  if (ABS(acc_y) < acc_tot_vect){
		  acc_pitch = asin(acc_y/acc_tot_vect) * 57.288;
	  }
	  if (ABS(acc_x) < acc_tot_vect){
	  		  acc_roll = asin(acc_x/acc_tot_vect) * -57.288; // negative to ensure left wing up is +roll
	  	  }

	  roll = (roll*0.9995) + (acc_roll*0.0005);
	  pitch = (pitch*0.99955) + (acc_pitch*0.0005);
	  yaw = gy_yaw;



	  roll_al = roll * 3;
	  pitch_al = pitch * 3;

	 // HC_SR04_Read();

	  Calculate_SetPoints();
	  Calculate_PIDs();

	  // function to read in values stored in the ESP32 UART DMA

	  //  Function to check fault flags
	  //Check_Faults();

	  // check to see if arm switch is disarmed
	  if (channel[4] < 1500 || channel[4] == 0){
		  flight_state = idle;
		  armed = 0;
	  }

	  // State machine for the drone switch case
	  switch (flight_state){
	  case(idle):
			// Ensure motors are not running
			TIM4->CCR1 = 0;
			TIM4->CCR2 = 0;
			TIM4->CCR3 = 0;
			TIM4->CCR4 = 0;
			// Wait for receiver connection
			if (rx_buff[0] == 0x20 & armed == 0 & (channel[4] > 1500) & (channel[2] < 1030)){
				flight_state = arming;
			}
			// need to check this is the right channel
			else if (channel[5] > 1600 & armed == 1 & channel[4] > 1500){
				 flight_state = rate_mode;
			 }
	  	  	// controller runs 250 times a second so mod 125 so the LED flashes every 500ms
	  	  	// blink Top orange LED
			if(loopcounter % 125 == 0){
				HAL_GPIO_TogglePin(GPIOC, o_led_Pin);
			}
		  break;

	  case(arming):
		  // send 1000us ESC pulses
		  if (armed == 0){
			  TIM4->CCR1 = 1000;
			  TIM4->CCR2 = 1000;
			  TIM4->CCR3 = 1000;
			  TIM4->CCR4 = 1000;
			  HAL_Delay(3000);
			  armed ++;
			  flight_state = idle;
	      }

		  break;

	  case(rate_mode):
		  Update_Motors();
		  break;

	  case(auto_level):
		  break;

	  case(altitude_hold):
		  break;

	  case(error):
		  // Alternately blink orange and red LED
		  if(loopcounter % 125 == 0){
			  HAL_GPIO_WritePin(GPIOC, o_led_Pin, RESET);
			  HAL_GPIO_WritePin(GPIOC, o_led_Pin, SET);
		  }
	      if(loopcounter % 75 == 0){
	    	  HAL_GPIO_WritePin(GPIOC, r_led_Pin, SET);
	    	  HAL_GPIO_WritePin(GPIOC, r_led_Pin, RESET);
	      }
		  // Ensure motors are not running
		  TIM4->CCR1 = 0;
		  TIM4->CCR2 = 0;
		  TIM4->CCR3 = 0;
		  TIM4->CCR4 = 0;

	      break;
	  }

	  // ensure the loop happens every 4ms
	  while(TIM1->CNT < 4000){
	  };
	  looptimmer = TIM1->CNT;
	  if (looptimmer > 4300){
		  error_counter ++;
		  if(error_counter > 3){
			  //flight_state = error;
		  }
	  }
	  TIM1->CNT = 0;

  }
  /* USER CODE END 3 */
}

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
/* USER CODE BEGIN 4 */

float ABS(float x){
	if(x > 0){
		return x;
	}
	else{
		return (-x);
	}

}

HAL_StatusTypeDef ICM20689_Read(uint8_t address, float *acc_x, float *acc_y, float *acc_z, float *temp,
		float *gy_x, float *gy_y, float *gy_z, float gy_cal_x, float gy_cal_y, float gy_cal_z, float acc_cal_x, float acc_cal_y, float acc_cal_z)
{
	HAL_StatusTypeDef ret;
	// Bytes to store the incoming accelerometer data
	uint8_t acc_data[6];
	int16_t acc_s_data[3];

	// Bytes to store the incoming temperature data
	uint8_t temp_data[2];
	int16_t temp_s_data;

	// Bytes to store the incoming gyroscope data
	uint8_t gy_data[6];
	int16_t gy_s_data[3];

	// Reading Accelerometers registers
	ret = HAL_I2C_Mem_Read(&hi2c2, (uint16_t)(address<<1)| 0x01, 0x3B , 1, acc_data, 6, 50);
	if(ret != HAL_OK)
	{
		return ret;
	}

	ret = HAL_I2C_Mem_Read(&hi2c2, (uint16_t)(address<<1)| 0x01, 0x41 , 1, temp_data, 2, 50);
	if(ret != HAL_OK)
	{
		return ret;
	}

	ret = HAL_I2C_Mem_Read(&hi2c2, (uint16_t)(address<<1)| 0x01, 0x43 , 1, gy_data, 6, 50);
	if(ret != HAL_OK)
	{
		return ret;
	}

	// Shift and combine the 2 accelerometer registers per axis and store them in a signed 16 int
	acc_s_data[0] = (acc_data[0]<<8 | acc_data[1]);
	acc_s_data[1] = (acc_data[2]<<8 | acc_data[3]);
	acc_s_data[2] = (acc_data[4]<<8 | acc_data[5]);

	// Normalise the accelerations by the sensitivity/g
	*acc_x =  (acc_s_data[0] / 4096.0) - acc_cal_x;
	*acc_y = (acc_s_data[1] / 4096.0) - acc_cal_y;
	*acc_z = (acc_s_data[2] / 4096.0) - acc_cal_z ;

	// Shift and combine the 2 temperature registers and store them in a signed 16 int
	temp_s_data = (temp_data[0]<<8 | temp_data[1]);

	// Normalise the temperature values
	*temp = ((temp_s_data - 0)/326.8) + 25;

	// Shift and combine the 2 gyroscope registers per axis and store them in a signed 16 int
	gy_s_data[0] = (gy_data[0]<<8 | gy_data[1]);
	gy_s_data[1] = (gy_data[2]<<8 | gy_data[3]);
	gy_s_data[2] = (gy_data[4]<<8 | gy_data[5]);

	// Normalise the gyroscope by the sensitivity/g
	*gy_x =  ((gy_s_data[0] /32.8 ) - gy_cal_x);
	*gy_y = ((gy_s_data[1] / 32.8 ) - gy_cal_y);
	*gy_z = ((gy_s_data[2] / 32.8 ) + gy_cal_z) * -1; // Invert Z axis / yaw to match convention (Nose right = positive yaw)


	return HAL_OK;
}

HAL_StatusTypeDef ICM20689_Config(uint8_t address, float *gy_cal_x, float *gy_cal_y, float *gy_cal_z, float *acc_cal_x, float *acc_cal_y, float *acc_cal_z)
{
	HAL_StatusTypeDef ret;
	uint8_t config_pwr = 0x81;
	uint8_t config_pwr1 = 0x00;
	uint8_t whoami;
	uint8_t config = 0x10; // configure gyroscope and accelerometer to full scale
	uint8_t config_lowpass = 0x03;
	uint8_t rst = 0x01;
	uint16_t i; //calibration counter

	// temporary ICM20689 variables
	float t_acc_x, t_acc_y, t_acc_z;
	float t_temp;
	float t_gy_x, t_gy_y, t_gy_z;

	// gyroscope errors
	float gy_er_x = 0, gy_er_y = 0, gy_er_z = 0;

	// accelerometer errors
	float acc_er_x = 0, acc_er_y = 0, acc_er_z = 0;



	// Soft Reset
	ret = HAL_I2C_Mem_Write(&hi2c2, (uint16_t)(address<<1), 0x6B, 1, &config_pwr, 1, 50);
	if(ret != HAL_OK){
		return ret;
	}
	HAL_Delay(100);

	// Wake up
	ret = HAL_I2C_Mem_Write(&hi2c2, (uint16_t)(address<<1), 0x6B, 1, &config_pwr1, 1, 50);
	if(ret != HAL_OK){
		return ret;
	}
	HAL_Delay(100);

	// Check to see if icm20689 is responding correctly
	ret = HAL_I2C_Mem_Read(&hi2c2, (uint16_t)(address<<1)|  0x01 , 0x75, 1, &whoami, 1, 50);
	if(ret != HAL_OK){
		return ret;
	}
	if(whoami == 0x98){
		HAL_GPIO_TogglePin(GPIOC, r_led_Pin);
		HAL_Delay(500);
		HAL_GPIO_TogglePin(GPIOC, r_led_Pin);
	}

	// Configure the accelerometer
	ret = HAL_I2C_Mem_Write(&hi2c2, (uint16_t)(address<<1), 0x1C, 1, &config, 1, 50);
	if(ret != HAL_OK){
		return ret;
	}

	// Configure the accelerometer Filter
	ret = HAL_I2C_Mem_Write(&hi2c2, (uint16_t)(address<<1), 0x1D, 1, &config_lowpass, 1, 50);
			if(ret != HAL_OK){
				return ret;
				}

	// Configure the gyroscope
	ret = HAL_I2C_Mem_Write(&hi2c2, (uint16_t)(address<<1), 0x1B, 1, &config, 1, 50);
		if(ret != HAL_OK){
			return ret;
		}

	// Configure the gyroscope Filter
	ret = HAL_I2C_Mem_Write(&hi2c2, (uint16_t)(address<<1), 0x1A, 1, &config_lowpass, 1, 50);
	if(ret != HAL_OK){
		return ret;
		}

	// Reset gyroscope and accelerometer registers
	ret = HAL_I2C_Mem_Write(&hi2c2, (uint16_t)(address<<1), 0x6A, 1, &rst, 1, 50);
	if(ret != HAL_OK){
		return ret;
		}


	for (i=0; i < 2000; i++)
	{
		ICM20689_Read(address, &t_acc_x, &t_acc_y, &t_acc_z, &t_temp, &t_gy_x, &t_gy_y, &t_gy_z, 0, 0, 0, 0, 0, 0);
		gy_er_x += t_gy_x;
		gy_er_y += t_gy_y;
		gy_er_z += t_gy_z;
		acc_er_x += t_acc_x;
		acc_er_y += t_acc_y;
		acc_er_z += t_acc_z;
		HAL_Delay(4);
		if (i % 125 == 0){
			HAL_GPIO_TogglePin(GPIOC, o_led_Pin);
		}
	}
	// store average calibration;
	*gy_cal_x = gy_er_x / 2000;
	*gy_cal_y = gy_er_y / 2000;
	*gy_cal_z = gy_er_z / 2000;
	*acc_cal_x = acc_er_x / 2000;
	*acc_cal_y = acc_er_y / 2000;
	*acc_cal_z = (acc_er_z - 2000) / 2000;

	return HAL_OK;

}

void Update_Motors(){
	// Variable to store throttle value
	uint16_t throttle = channel[2];

	if (throttle > 1800){throttle = 1800;} //limit max throttle to allow for some room for the PIDs to still correct.

	// ESC1 | CCR1 | Front Right | CW
	// ESC2 | CCR2 | Rear Right  | CCW
	// ESC3 | CCR3 | Front Left  | CCW
	// ESC4 | CCR4 | Rear Left   | CW
	// Channel[2] = Throttle

	// test difference between ESC variables being floats and ints

	esc_1 = throttle - pid_output_pitch + pid_output_roll + pid_output_yaw;
	esc_2 = throttle + pid_output_pitch + pid_output_roll - pid_output_yaw;
	esc_3 = throttle - pid_output_pitch - pid_output_roll - pid_output_yaw;
	esc_4 = throttle + pid_output_pitch - pid_output_roll + pid_output_yaw;

	if (esc_1 > 2000){esc_1 = 2000;}
	//if (esc_1 < motor_idle){esc_1 = motor_idle;}

	if (esc_2 > 2000){esc_2 = 2000;}
	//if (esc_2 < motor_idle){esc_2 = motor_idle;}

	if (esc_3 > 2000){esc_3 = 2000;}
	//if (esc_3 < motor_idle){esc_3 = motor_idle;}

	if (esc_4 > 2000){esc_4 = 2000;}
	//if (esc_4 < motor_idle){esc_4 = motor_idle;}

	TIM4->CCR1 = esc_1;
	TIM4->CCR2 = esc_2;
	TIM4->CCR3 = esc_3;
	TIM4->CCR4 = esc_4;


}

void Calculate_PIDs(){

	//Roll - Y - Channel[0]
	float temp_err = 0;
	temp_err = pid_gy_roll - pid_setpoint_roll;
	pid_integ_roll += pid_i_roll * temp_err;
	if (pid_integ_roll > max_rotate){pid_integ_roll = max_rotate;}
	if (pid_integ_roll < (max_rotate*-1)){pid_integ_roll = (max_rotate*-1);}

	pid_output_roll = (pid_p_roll * temp_err) + (pid_integ_roll) + (pid_d_roll * (temp_err - pid_prev_err_roll));
	if (pid_output_roll > max_rotate){pid_output_roll = max_rotate;}
	if (pid_output_roll < (max_rotate*-1)){pid_output_roll = (max_rotate*-1);}

	pid_prev_err_roll = temp_err;

	//Pitch - X - Channel[1]
	temp_err = 0;
	temp_err = pid_gy_pitch - pid_setpoint_pitch;
	pid_integ_pitch += pid_i_roll * temp_err;
	if (pid_integ_pitch > max_rotate){pid_integ_pitch = max_rotate;}
	if (pid_integ_pitch < (max_rotate*-1)){pid_integ_pitch = (max_rotate*-1);}

	pid_output_pitch = (pid_p_roll * temp_err) + (pid_integ_pitch) + (pid_d_roll * (temp_err - pid_prev_err_pitch));
	if (pid_output_pitch > max_rotate){pid_output_pitch = max_rotate;}
	if (pid_output_pitch < (max_rotate*-1)){pid_output_pitch = (max_rotate*-1);}

	pid_prev_err_pitch = temp_err;

	//Yaw - Z - Channel[3]
	temp_err = 0;
	temp_err = pid_gy_yaw - pid_setpoint_yaw;
	pid_integ_yaw += pid_i_yaw * temp_err;
	if (pid_integ_yaw > max_rotate){pid_integ_yaw = max_rotate;}
	if (pid_integ_yaw < (max_rotate*-1)){pid_integ_yaw = (max_rotate*-1);}

	pid_output_yaw = (pid_p_yaw * temp_err) + (pid_integ_yaw) + (pid_d_yaw * (temp_err - pid_prev_err_yaw));
	if (pid_output_yaw > max_rotate){pid_output_yaw = max_rotate;}
	if (pid_output_yaw < (max_rotate*-1)){pid_output_yaw = (max_rotate*-1);}

	pid_prev_err_yaw = temp_err;
}

void Calculate_SetPoints(){

	//Roll - Y - Channel[0]
	if (channel[0] != 0){
		pid_setpoint_roll = 0;
		if (channel[0] > 1505){pid_setpoint_roll = (channel[0] - 1505)/3;} 	// max 495
		if (channel[0] < 1495){pid_setpoint_roll = (channel[0] - 1495)/3;} 	// max -495
		pid_setpoint_roll -= (roll_al);										// Max angular rate of 247
	}
	else {
		pid_setpoint_roll = 0;
	}

	//Pitch - X - Channel[1]
	if (channel[1] != 0){
		pid_setpoint_pitch = 0;
		if (channel[1] > 1505){pid_setpoint_pitch = (1505 - channel[1])/3;} // max 495
		if (channel[1] < 1495){pid_setpoint_pitch = (1495 - channel[1])/3;} // max -495
		pid_setpoint_pitch += pitch_al;									// Max angular rate of 247
	}
	else{
		pid_setpoint_pitch = 0;
	}
	//Yaw - Z - Channel[3]
	if (channel[3] != 0){
		if (channel[3] > 1505){pid_setpoint_yaw = (channel[3] - 1505)/3;} // max 495
		if (channel[3] < 1495){pid_setpoint_yaw = (channel[3] - 1495)/3;} // max -495
		// Max angular rate of 247
	}
	else{
		pid_setpoint_yaw = 0;
	}
}

void HC_SR04_Read(){

	// Reset the trigger pin and wait 3 micro seconds
	HAL_GPIO_WritePin(trig_GPIO_Port, trig_Pin, GPIO_PIN_RESET);
	uSec_Delay(3);

	// Take the trigger pin high for 10 micro seconds
	HAL_GPIO_WritePin(trig_GPIO_Port, trig_Pin, GPIO_PIN_SET);
	uSec_Delay(10);
	HAL_GPIO_WritePin(trig_GPIO_Port, trig_Pin, GPIO_PIN_RESET);

	// Start the echo input capture
	HAL_TIM_IC_Start_IT(&htim12, TIM_CHANNEL_1);

	//wait for the echo to be measured
	if (sr_rdy_flg == 1){
		//Reset Flag
		sr_rdy_flg = 0;
		// stop the input capture
		HAL_TIM_IC_Stop_IT(&htim12, TIM_CHANNEL_1);

		// Read in the echo pulse width
		if (echo_edge_2 > echo_edge_1){
			height = (float)(echo_edge_2 - echo_edge_1) * time_to_dist;
		}
		else{
			height = 0;
			fault_flag = 1;
		}

	}
}

void uSec_Delay(uint32_t uSec){
	if (uSec < 2){uSec = 2;}
	//Setup the timer
	TIM2->ARR = uSec - 1;
	TIM2->EGR = 1;
	TIM2->SR &= ~1;
	TIM2->CR1 |= 1;
	while((TIM2->SR & 0x0001) != 1);
	TIM2->SR &= ~(0x0001);
}

void Check_Faults(){

}

void HAL_TIM_IC_CaptureCalllback(TIM_HandleTypeDef *htim){
	if (capture_num == 0){
		echo_edge_1 = HAL_TIM_ReadCapturedValue(htim, TIM_CHANNEL_1);
		capture_num = 1;
	}
	else if (capture_num == 1){
		echo_edge_2 = HAL_TIM_ReadCapturedValue(htim, TIM_CHANNEL_1);
		capture_num = 0;
		sr_rdy_flg = 1;
	}
}

void HAL_UART_RxCpltCallback(UART_HandleTypeDef *huart3){
	uint8_t *ptr = huart3->pRxBuffPtr;
	uint8_t *ptrl;
	if (*ptr == 0x20){
		ptr += 2;
		ptrl = ptr+1;
		for (int8_t i  = 0; i < 10; i++){
			channel[i] = (*(ptrl+(i*2)) << 8) | *(ptr+(i*2));
		}

	}
}

/* USER CODE END 4 */
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


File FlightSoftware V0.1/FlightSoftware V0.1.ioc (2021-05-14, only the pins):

PH0-OSC_IN.Signal=RCC_OSC_IN
Mcu.UserName=STM32F405RGTx
PC10.Signal=USART3_TX
PB13.GPIO_Label=trig
PB11.Signal=I2C2_SDA
PB13.Signal=GPIO_Output
PC15-OSC32_OUT.GPIO_Label=r_led
PB6.Signal=S_TIM4_CH1
PB7.Signal=S_TIM4_CH2
PB9.Signal=S_TIM4_CH4
PC14-OSC32_IN.GPIO_Label=o_led
PC11.Signal=USART3_RX
PC14-OSC32_IN.Signal=GPIO_Output
PA13.Signal=SYS_JTMS-SWDIO
PC15-OSC32_OUT.Signal=GPIO_Output
PB10.Signal=I2C2_SCL
PB14.Signal=S_TIM12_CH1
PH1-OSC_OUT.Signal=RCC_OSC_OUT
PB3.Signal=SYS_JTDO-SWO
PA14.Signal=SYS_JTCK-SWCLK
PB8.Signal=S_TIM4_CH3

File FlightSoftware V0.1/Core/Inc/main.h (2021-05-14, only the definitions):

#define o_led_Pin GPIO_PIN_14
#define o_led_GPIO_Port GPIOC
#define r_led_Pin GPIO_PIN_15
#define r_led_GPIO_Port GPIOC
#define trig_Pin GPIO_PIN_13
#define trig_GPIO_Port GPIOB

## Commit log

2021-03-09 Added USB and JTAG
    [FYP_Drone.SchLib, STM32 Flight Controller.PrjPcb, Top Level.SchDoc]
2021-03-10 USB and JTAG footprints
    [FYP_Drone.PcbLib, FYP_Drone.SchLib, STM32 Flight Controller.PrjPcb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]
2021-03-10 added USBLC-2sC6 Footprint
    [FYP_Drone.PcbLib, Top Level.SchDoc]
2021-03-12 Schematics updated
    [FYP_Drone.PcbLib, FYP_Drone.SchLib, Top Level.SchDoc]
2021-03-14 Added component links, connectors and start of sensors
    [Connectors and USB.SchDoc, FYP_Drone.PcbLib, FYP_Drone.SchLib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]
2021-03-20 Added Templates
    [Connectors and USB.SchDoc, STM32.SchDoc, Sensors.SchDoc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]
2021-03-22 added ICM-20689
    [FYP_Drone.PcbLib, FYP_Drone.SchLib]
2021-03-22 Added Ultra sound and ICM -20689
    [FYP_Drone.SchLib, STM32.SchDoc, Sensors.SchDoc]
2021-03-23 Updated template and changed GPS and compass coneectors
    [Connectors and USB.SchDoc, FYP_Drone.PcbLib, Power Regulation.SchDoc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]
2021-03-23 Project FIle
    [STM32 Flight Controller.PrjPcb]
2021-03-23 Updated all footprints and added power regulation
    [Connectors and USB.SchDoc, FYP_Drone.PcbLib, FYP_Drone.SchLib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]
2021-03-25 Started PCB layout and routing
    [Connectors and USB.SchDoc, FYP_Drone.PcbLib, Power Regulation.SchDoc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]
2021-03-26 Added Silk
    [Sensors.SchDoc]
2021-03-26 Finalised Power Regulation layout
2021-03-27 Nearly final route
    [Connectors and USB.SchDoc]
2021-03-29 Created Gerber Files
    [Connectors and USB.SchDoc, Power Regulation.SchDoc, STM32 Flight Controller.PrjPcb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]
2021-03-29 Added BOM
    [STM32 Flight Controller.xlsx]
2021-05-12 Added Pdfs
    [Connectors and USB.SchDoc, Power Regulation.SchDoc, STM32 Flight Controller.PrjPcb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]
2021-06-05 Added Schematic photos

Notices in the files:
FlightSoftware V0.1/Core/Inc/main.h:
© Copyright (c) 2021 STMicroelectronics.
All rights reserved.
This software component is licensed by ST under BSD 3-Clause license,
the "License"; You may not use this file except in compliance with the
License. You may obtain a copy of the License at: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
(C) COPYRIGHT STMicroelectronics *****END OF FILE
